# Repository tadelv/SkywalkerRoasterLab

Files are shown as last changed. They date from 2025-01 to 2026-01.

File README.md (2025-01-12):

# Skywalker Roaster

This is a guide to for connecting the Skywalker/ITOP MTCR(SkItop) Roaster connected to Artisan. In addition to the arduino sketches the data I've collected about the roaster is available here.

⚠️WARNING 👉 DO NOT LEAVE ROASTER UNATTENDED⚠️

The easiest way to get this working is to
1. Connect USB cable to [Arduino](#arduino-instructions) with correct jumpers
2. Load [Sketch](#arduino-instructions) onto arduino
3. Load [config[](#artisan-upload-config) into artisan-scope
4. Plug in arduino to computer through arduino USB cable(NOT the one we jumpered)
5. Plug in arduino to roaster where the controller was connected with the USB cable we jumpered
6. In artisan [config](#artisan-manually-setting-config) set the correct device
7. click/tap the on button in artisan-scope and temps should be available and roaster is controllable
   
## Arduino Sketches

### SkyCommand
This is full control of the skywalker roaster via Artisan. The sketch does the bare minimum to emulate TC4. Exercise caution, there are minimal safety features built in. As with every other coffee roaster..

⚠️WARNING 👉 DO NOT LEAVE ROASTER UNATTENDED⚠️

The sketch requires that it see a command from Artisan at least every 10 seconds or it will shut down. The READ commands from artisan will keep it going. I think it's ok to run, but what do I know? I'm just a nerd on the internet. Use this at your own risk.

#### Hardware
I use an arduino leonardo with a USB cable soldered to the Vin, GND, and Digital Pins 2 and 3. That's it.
PXL_20231206_190446798 MP

The black cable goes to the USB port on the back of the roaster (that's only USB in form.. it's not actually using USB communications), the white one to my computer running Artisan.

## Arduino Instructions

1. Install ArduinoIDE

2. Find any old USB cable. Cut it up in half, and prune a bit off the plastic sleeving. You should find four smaller wires. Connect these wires to your Arduino as such either through soldering or just inserting it into the slots:

      Green -> Digital 2  
      White -> Digital 3  
      Red -> VIN  
      Black -> GND

    Breadboard example:
   
    

    Soldering example (more secure):
   
    
    
    
3. Download repository and extract.


1. Connect your Arduino into your computer.

    

2. Go to your SkywalkerRoaster-main folder that you extracted. Click on the SkyCommand folder then double click on `SkyCommand.ino` (should open automatically in ArduinoIDE)

3. Click on the check mark to do a precompile, this lets you know if the code will work on your board.
4.  Click on your Arduino device and press Upload, the console on the bottomr should give you a success message. Some boards output debug, but if there is no error it probably succeeded.


## Hardware Pinout Examples
Arduino Micro
<!-- <img src="images/ardunio_micro_pinout.jpg" alt="micro pinout" width="400"/> -->


## Artisan Upload Config
We can upload a preset config in Artisan Scope
Help -> Load Settings...


This is a default file with the most basic settings.
[basic-skitop-artisan-settings.aset](ArtisanConfigs/basic-skitop-artisan-settings.aset)

look in [ArtisanConfigs](ArtisanConfigs/) for other configs users have created.

## Artisan Manually Setting Config
Here's how I have Artisan configured.
Config -> Device


After pressing OK, an additional dialogue box will appear, select your Arduino. If you're not sure which is your Arduino, disconnect and reconnect it and the dialogue box should change.
You can also navigate here by going to Config -> Port...
Comm Port will be different depending on OS you are running and which USB port you are plugged into.



Config -> Events -> Config

```
DRUM;100
```

Config -> Events -> Buttons

```
DRUM;100
```
```
DRUM;0
```
```
FILTER;1
```
etc..

Config -> Events -> Sliders

```
OT2;{}
```
```
OT1;{}
```
### Troubleshooting
- check all connections, unplug and re-plug in the USB cables, also check pins and solder points
- swap out USB cables, the arduino to computer cable is important also
- you will need to have drivers for your arduino unit on some machines so if you're running on a different machine where you set up the arduino, just install arduino IDE and install the drivers with the IDE to ensure you can connect
- make sure you are on the tested or later version of artisan

### Testing/Compatibility
#### Artisan Version
- 2.10.2
#### Working Hardware Combos
- Leonardo
  - Windows ?
- Micro
  - Windows 11
  - MacOS
- Nano ATMEGA
  - Linux Mint

- Uno Wifi R4
  - not yet

### SkywalkerSpy
This provides logging only for Artisan. It uses two pins to monitor the Tx lines from both the roaster and the controller. It alternates between reading the values as quickly as possible. When any input comes in on the serial line the sketch will respond with the status of the roaster in the format TEMP,HEAT DUTY,VENT DUTY

## Roaster Hardware
This has been super fun to study. Here's what I've learned so far.

The controller has a [js32t031f5s7 microcontoller](http://www.honor-ic.com/Product/ProScreenDetail?pid=118).

I am unsure what kind of microcontroller is inside the roaster. It is marked FMD N3hWIKH and I was unable to locate any datasheets for it.



The roaster uses a thermistor as a temperature probe which is connected to the microcontroller as shown here.



It appears to use a voltage divider with two taps, one passing through a 1k resistor and the other through a 2k resistor. I'm not the strongest hardware guy by any means, but I don't understand why. If this look familiar to you, please let me know what we're looking at here.

### Normal Operation
The Skywalker roaster is rather simple all logic lives in the controller. The roaster simply interprets the signals sent by the controller and sets things accordingly. The roaster appears to shut down if it does not receive a control message in 1 second. The controller reads the temperature values from the roaster and then sends instructions to the roaster. There does not appear to be any kind of communications protocol, each device appears to send messages to the other device roughly every 10 milliseconds. There are no requests, responses, acknowledgements, etc..  Simply data bit banged on a GPIO line.

## Messages
The messages sent by each device are rather simple in structure. I've determined what most everything does. To the logic analyzer, the messages appear as follows. This is an example of the message the roaster sends. The controller's messages look identical other than being 8 bits shorter.



Interpreting the messages can be done by simply measuring the logic LOW pulses. The beginning preamble is roughly 7.5ms, a binary 1 is represented by a ~1.5ms pulse, a binary 0 is ~600 microseconds, and the logic HIGH between bits is roughly 750 microseconds.



### Controller
The controller transmits a 6 byte message in LSB order. Both messages contain a checksum and will be ignored if the checksum is not correct.

| Position | Purpose | Value |
|---|---|---|
| 0 | Fan Duty Cycle | 0 to 100
| 1 | Filter | Appears to only be values 0,1,2,3,4 |
| 2 | Bean Cooling Fan | 0 or 100 |
| 3 | Drum | 0 or 100 |
| 4 | Heater Duty Cylce | 0 to 100 |
| 5 | Checksum | |

For the Fan and Heater, duty cycles increment by 5. Sending other values will be ignored.

### Roaster
The roaster transmits a 7 byte message in LSB Order.
|Position| Name| Value|
|---|-----|---|
|0,1| Value A | I'm not _really_ sure what this value is. I suspect it is perhaps a voltage as read by an ADC on the microcontroller|
|2,3|Value B|Again, not _really_ sure what the value really represents. I think it is another ADC value.|  
| 4 | Mystery byte | Always a 0.|
| 5 | Mystery byte | Pretty much always a 1. I've not seen much of a correlation to hardware that seems to indicate what this may represent.|
|6 | Checksum||

Value A and Value B are my biggest open question about this roaster. What is it doing?! There is a very strong linear correlation between the two values and the temperature displayed on the controller screen. However I could not determine what I would consider to be an "elegant" solution for converting these values to the temperature. Rather, I fit a 4th degree polynomial to the data (see `data/model3.py` but please keep in mind it's been a long minute since I've run a regression. ChatGPT wrote a lot of that with some guidance.)

To collect the data I attached a logic probe to the controller and captured a preheat cycle. I extracted all the messages from the capture, wrote an arduino sketch to replay the bytes in the messages back to the controller, and coded up a quick and dirty python script to push each message to the arduino and allow me to enter the value shown on the screen. The results of this process are in `Data/RealLabeledTemperatures.txt`

### Other Observations
- The roaster is looking for a USB ground, if nothing is there it will not run, if you unplug the controller or arduino during a roast, everything shuts down, this is actually kind of dangerous as the beans inside could ignite without movement or fan.
- Some testing unplugging the signal pins in the arduino yielded that the roaster will not run without constant signals from these pins either, but the user can plug back in and start controlling the roaster again. (granted you don't hit the 10sec limit from the sketch)

# Discord

There's a skywalker specific discord (not mine) that seems to have a small but growing and enthusiastic group. I'm on there. Come share your experiences with this roaster. [Skywalker Roaster Community](https://discord.gg/m4TtNRb4uc)

# Bug Fixes and Improvements

I'll spend some more time on things when I can, but pull requests are always welcome and appreciated.

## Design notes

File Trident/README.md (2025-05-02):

# Trident for Skywalker

Combines BLE, USB and WiFi access to the Skywalker roaster in one controller.

# Supported boards:

[ESP32-S3 devkitc 1 (dual usb-c)](https://a.aliexpress.com/_EH8OGvc)

# BLE setup
Use HiBean to connect to Trident. Search for "Skywalker-Trident" when adding the roaster in HiBean app.

# USB setup
Use the left usb-c port (when the board is facing you, usb ports facing down), to connect it to your computer. Use one
of the provided `.aset` Artisan settings in the "Artisan Config" folder, to connect to the roaster. Remember to select the correct port in Artisan!

# Wifi setup
At first start, Trident creates an access point with the SSID "Trident". Once you connect to it, you can use the
provided artisan config (in this folder) and it should connect automatically.

If you wish to setup Trident to connect to your home Wifi, you can set it up using a simple curl command or by visiting
the address in the browser:
```
curl http://trident.local/api/wifi?ssid=<your-wifi>&pass=<your-pass>
```

This will save the wifi ssid and credentials to Trident persistent storage. Now you can reboot/reset Trident and it will
connect to your Wifi automatically. 
If Trident can't find the specified Wifi or the password is incorrect, it will create the previously mentioned access
point, so that you can change the wifi data again.

# Simultaneous operation
While not entirely sensible, simultaneous operation is theoretically possible with Trident. You could for example
observe and control the roast, both from HiBean and Artisan at the same time.

# TODO list:

- PID control
- LED status signalling
- code cleanup and potential improvements

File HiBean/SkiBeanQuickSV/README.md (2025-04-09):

# PID Commands - HiBean ESP32 BLE Roaster Control

This document lists the available commands for controlling the roaster using PID_v1 in the HiBean ESP32 BLE Roaster Control firmware.

## **PID Commands & Behavior**
The **PID_v1** library is used to regulate heating power based on the measured temperature. It operates in **two modes**:
- **Automatic (PID ON):** Uses PID logic to adjust the heater output.
- **Manual (PID OFF):** Allows manual control of heater power.

## **Available Commands (case-INsensitive)**
| **Command** | **Description** |
|---|---|
| `PID;ON` | Enables PID control (automatic mode). |
| `PID;OFF` | Disables PID control (switches to manual mode). |
| `PID;SV;XXX` | Sets the PID **setpoint temperature** (XXX is in °C, e.g., `PID;SV;250` sets the target to 250°C). |
| `PID;T;PP.P;II.I;DD.D` |  Apply provided tunings to the PID control (not persisted). |
| `PID;CT;XXX` | Temporarily sets PID cycle (sample) time to XXXms (not persisted). |
| `PID;PM;E` | Temporarily change pMode: E = P_ON_E to M = P_ON_M(default), or reverse (not persisted). |
| `OT1;XX` | Manually sets heater power to **XX%** (only works in MANUAL mode). |
| `READ` | Retrieves current temperature, set temperature, heater, and vent power. |

## **Other Control Commands**
| **Command** | **Description** |
|---|---|
| `OT2;XX` | Sets the vent power to **XX%**. |
| `OFF` | Shuts down the system. |
| `ESTOP` | Emergency stop: Sets heater to 0% and vent to 100%. |
| `DRUM;XX` | Starts/stops the drum motor (1 = ON, 0 = OFF). |
| `FILTER;XX` | Controls filter fan power (1 fastest - 4 slowest; 0 off). |
| `COOL;XX` | Activates cooling function (0-100%). |
| `CHAN` | Sends active channel configuration. |
| `UNITS;C/F` | Sets temperature units to **Celsius (C)** or **Fahrenheit (F)**. |

## **Usage Example**
- Enable PID control:
  ```
  PID;ON
  ```
- Set target temperature to 250°C:
  ```
  PID;SV;250
  ```
- Manually set heater to 70% power:
  ```
  OT1;70
  ```
- Read current system status:
  ```
  READ
  ```

This document serves as a quick reference for controlling the roaster over BLE using the HiBean ESP32 BLE Roaster Control firmware.

TODO
- ~~BLE on Core1~~
- PID storage via Preference
- sTune Autotune Function
- RTD Max31865 Implementation
- TC Max31855 Implementation
- AutoDrop Servo

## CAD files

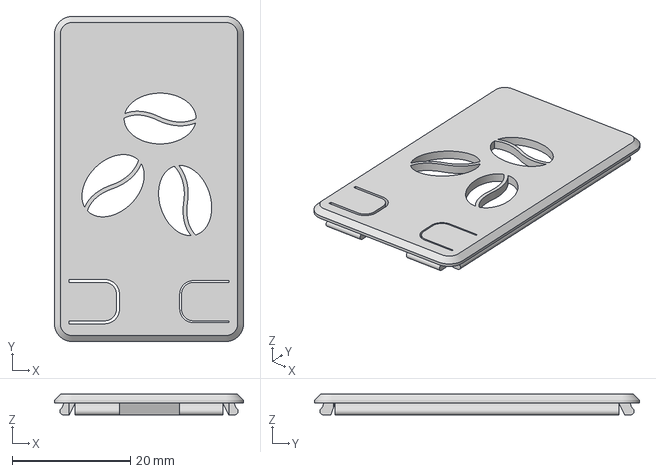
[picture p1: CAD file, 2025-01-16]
HiBean/3DP Case/SkiBeanMiniLid.3mf
32.0 x 55.0 x 3.50 mm

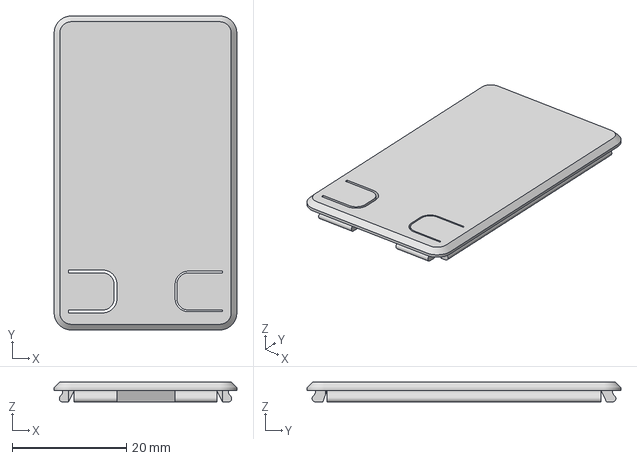
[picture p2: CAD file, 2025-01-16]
HiBean/3DP Case/SkiBeanMiniLid_nobnz.3mf
32.0 x 55.0 x 3.50 mm

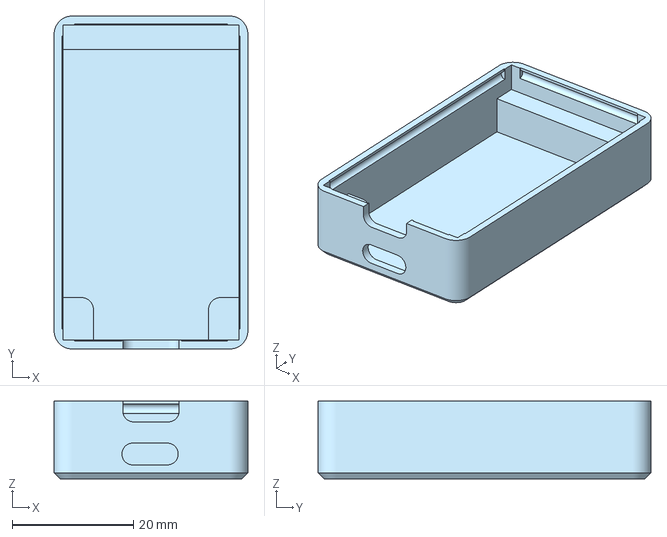
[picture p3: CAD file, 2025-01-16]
HiBean/3DP Case/SkiBeanMiniCase.3mf
32.0 x 55.0 x 12.8 mm

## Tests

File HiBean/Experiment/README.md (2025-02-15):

# QuickPID Commands - HiBean ESP32 BLE Roaster Control

This document lists the available commands for controlling the roaster using QuickPID in the HiBean ESP32 BLE Roaster Control firmware.

## **PID Commands & Behavior**
The **QuickPID** library is used to regulate heating power based on the measured temperature. It operates in **two modes**:
- **Automatic (PID ON):** Uses PID logic to adjust the heater output.
- **Manual (PID OFF):** Allows manual control of heater power.

## **Available Commands**
| **Command** | **Description** |
|---|---|
| `PID;ON` | Enables PID control (automatic mode). |
| `PID;OFF` | Disables PID control (switches to manual mode). |
| `PID;SV;XXX` | Sets the PID **setpoint temperature** (XXX is in °C, e.g., `PID;SV;250` sets the target to 250°C). |
| `OT1;XX` | Manually sets heater power to **XX%** (only works in MANUAL mode). |
| `READ` | Retrieves current temperature, set temperature, heater, and vent power. |

## **Other Control Commands**
| **Command** | **Description** |
|---|---|
| `OT2;XX` | Sets the vent power to **XX%**. |
| `OFF` | Shuts down the system. |
| `ESTOP` | Emergency stop: Sets heater to 0% and vent to 100%. |
| `DRUM;XX` | Starts/stops the drum motor (1 = ON, 0 = OFF). |
| `FILTER;XX` | Controls filter fan power (0-100%). |
| `COOL;XX` | Activates cooling function (0-100%). |
| `CHAN` | Sends active channel configuration. |
| `UNITS;C/F` | Sets temperature units to **Celsius (C)** or **Fahrenheit (F)**. |

## **Usage Example**
- Enable PID control:
  ```
  PID;ON
  ```
- Set target temperature to 250°C:
  ```
  PID;SV;250
  ```
- Manually set heater to 70% power:
  ```
  OT1;70
  ```
- Read current system status:
  ```
  READ
  ```

This document serves as a quick reference for controlling the roaster over BLE using the HiBean ESP32 BLE Roaster Control firmware.

TODO
- BLE on Core1
- PID storage via Preference
- sTune Autotune Function
- RTD Max31865 Implementation
- TC Max31855 Implementation
- AutoDrop Servo

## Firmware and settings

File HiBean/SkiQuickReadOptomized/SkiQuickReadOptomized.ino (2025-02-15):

/***************************************************

HiBean ESP32 BLE Roaster Control

Replaces Classic Bluetooth with BLE (NUS).

Service UUID:

6e400001-b5a3-f393-e0a9-e50e24dcca9e

Characteristics UUIDs:

Write Characteristic (RX):


6e400002-b5a3-f393-e0a9-e50e24dcca9e

Notify Characteristic (TX):


6e400003-b5a3-f393-e0a9-e50e24dcca9e

Sends notifications for temperature/status data.

Expects commands via the write characteristic.


***************************************************/

#include <Arduino.h>

#include <BLEDevice.h>

#include <BLEUtils.h>

#include <BLEServer.h>

#include <BLE2902.h>

#include <QuickPID.h>

#include <sTune.h>
#include <Preferences.h>  // For saving PID settings



// -----------------------------------------------------------------------------

// BLE UUIDs for Nordic UART Service

// -----------------------------------------------------------------------------

#define SERVICE_UUID           "6e400001-b5a3-f393-e0a9-e50e24dcca9e" // NUS service

#define CHARACTERISTIC_UUID_RX "6e400002-b5a3-f393-e0a9-e50e24dcca9e" // Write

#define CHARACTERISTIC_UUID_TX "6e400003-b5a3-f393-e0a9-e50e24dcca9e" // Notify

// -----------------------------------------------------------------------------

// BLE Globals

// -----------------------------------------------------------------------------

BLEServer* pServer = nullptr;

BLECharacteristic* pTxCharacteristic = nullptr;

bool deviceConnected = false;

TaskHandle_t bleTaskHandle;

bool tuningActive = false;

sTune* tuner; 

Preferences preferences;

// -----------------------------------------------------------------------------

// Pin Definitions

// -----------------------------------------------------------------------------

const int TX_PIN = 19;  // Output pin to roaster

const int RX_PIN = 20;  // Input pin from roaster

// -----------------------------------------------------------------------------

// Timing Constants

// -----------------------------------------------------------------------------

const int PREAMBLE        = 7000;

const int PULSE_ONE       = 1200;

const int PULSE_ZERO      = 650;

const int POST_PULSE_DELAY= 750;

const int START_PULSE     = 7500;

const int START_DELAY     = 3800;

// -----------------------------------------------------------------------------

// Buffer Sizes

// -----------------------------------------------------------------------------

const int ROASTER_LENGTH    = 7;   // 7 bytes received from roaster

const int CONTROLLER_LENGTH = 6;   // 6 bytes sent to roaster

// -----------------------------------------------------------------------------

// Control Byte Indices

// -----------------------------------------------------------------------------

enum ControlBytes {

VENT_BYTE = 0,

DRUM_BYTE = 3,

COOL_BYTE = 2,

FILTER_BYTE = 1,

HEAT_BYTE = 4,

CHECK_BYTE = 5

};

uint8_t receiveBuffer[ROASTER_LENGTH];

uint8_t sendBuffer[CONTROLLER_LENGTH];

// Raw temperature values

uint16_t rawTempX, rawTempY;

// Control Bytes & Checksum

void setControlChecksum() {

uint8_t sum = 0;

for (int i = 0; i < (CONTROLLER_LENGTH - 1); i++) {

    sum += sendBuffer[i];

}

sendBuffer[CHECK_BYTE] = sum;  // Correct use of CHECK_BYTE

}

void setValue(uint8_t* bytePtr, uint8_t value) {

*bytePtr = value;

setControlChecksum();

}

// -----------------------------------------------------------------------------

// Temperature Variables & Filter

// -----------------------------------------------------------------------------

double temp          = 0.0;           // Filtered temperature

unsigned long lastEventTime = 0;

const unsigned long LAST_EVENT_TIMEOUT = 10UL * 1000000UL; // 10 seconds (micros)

char CorF            = 'C';           // 'C' or 'F'

int filtWeight       = 80;            // Filter weight (Artisan default)

// Define PID variables

float setpoint = 250.0; // Desired temperature (adjustable)

float input, output;

double Kp = 15, Ki = 0.070, Kd = .060;

QuickPID myPID(&input, &output, &setpoint, Kp, Ki, Kd, QuickPID::pMode::pOnError, QuickPID::dMode::dOnMeas, QuickPID::iAwMode::iAwCondition, QuickPID::Action::direct);

int manualHeatLevel = 50;

// -----------------------------------------------------------------------------

// Command Strings

// -----------------------------------------------------------------------------

const String CMD_READ         = "READ";

const String CMD_HEAT         = "OT1";

const String CMD_VENT         = "OT2";

const String CMD_OFF          = "OFF";

const String CMD_DRUM         = "DRUM";

const String CMD_FILTER       = "FILTER";

const String CMD_COOL         = "COOL";

const String CMD_CHAN         = "CHAN";

const String CMD_UNITS        = "UNITS";

const String CMD_FILTER_WEIGHT= "FILT";

// -----------------------------------------------------------------------------

// Forward Declarations

// -----------------------------------------------------------------------------

void parseAndExecuteCommands(String input);

void executeCommand(String command, uint8_t value);

void shutdown();

void sendMessage();

void getRoasterMessage();

// -----------------------------------------------------------------------------

// BLE Server Callbacks

// -----------------------------------------------------------------------------

class MyServerCallbacks : public BLEServerCallbacks {

void onConnect(BLEServer* pServer) override {

deviceConnected = true;

Serial.println("BLE: Client connected.");

}

void onDisconnect(BLEServer* pServer) override {

deviceConnected = false;

Serial.println("BLE: Client disconnected. Restarting advertising...");

pServer->getAdvertising()->start();

}

};

// -----------------------------------------------------------------------------

// BLE Characteristic Callbacks

// -----------------------------------------------------------------------------

class MyCallbacks : public BLECharacteristicCallbacks {

void onWrite(BLECharacteristic* pCharacteristic) override {

String rxValue = String(pCharacteristic->getValue().c_str());



if (rxValue.length() > 0) {

  String input = String(rxValue.c_str());

  Serial.print("BLE Write Received: ");

  Serial.println(input);

  parseAndExecuteCommands(input);

}

}

};

// -----------------------------------------------------------------------------

// Utility Functions

// -----------------------------------------------------------------------------

bool itsbeentoolong() {

unsigned long now = micros();

unsigned long duration = now - lastEventTime;

return (duration > LAST_EVENT_TIMEOUT);

}

void notifyClient(const String& message) {
    static unsigned long lastNotify = 0;
    const unsigned long notifyInterval = 250; // 500ms delay

    if (millis() - lastNotify >= notifyInterval) {
        lastNotify = millis();
        
        Serial.println("Attempting to notify BLE client with: " + message);
        if (deviceConnected && pTxCharacteristic) {
            pTxCharacteristic->setValue(message.c_str());
            pTxCharacteristic->notify();
            Serial.println("Notification sent successfully.");
        } else {
            Serial.println("Notification failed. Device not connected or TX characteristic unavailable.");
        }
    }
}


void shutdown() {

Serial.println("Shutting down...");

for (int i = 0; i < CONTROLLER_LENGTH; i++) {

    sendBuffer[i] = 0;

}

sendBuffer[CHECK_BYTE] = 0; // Reset checksum

}

void sendMessage() {

// Start pulse

pulsePin(TX_PIN, START_PULSE);

delayMicroseconds(START_DELAY);



// Send each byte, bit by bit

for (int i = 0; i < CONTROLLER_LENGTH; i++) {

    for (int j = 0; j < 8; j++) {

        if (bitRead(sendBuffer[i], j) == 1) {

            // '1' bit

            pulsePin(TX_PIN, 1500);

        } else {

            // '0' bit

            pulsePin(TX_PIN, PULSE_ZERO);

        }

        delayMicroseconds(POST_PULSE_DELAY);

    }

}

}

void bleTask(void* parameter) {

Serial.println("Starting BLE task on Core 0...");



BLEDevice::init("ESP32_Skycommand_BLE");

BLEDevice::setMTU(250);



pServer = BLEDevice::createServer();

pServer->setCallbacks(new MyServerCallbacks());



BLEService* pService = pServer->createService(SERVICE_UUID);



pTxCharacteristic = pService->createCharacteristic(

    CHARACTERISTIC_UUID_TX,

    BLECharacteristic::PROPERTY_NOTIFY | BLECharacteristic::PROPERTY_READ

);

pTxCharacteristic->addDescriptor(new BLE2902());



BLECharacteristic* pRxCharacteristic = pService->createCharacteristic(

    CHARACTERISTIC_UUID_RX,

    BLECharacteristic::PROPERTY_WRITE | BLECharacteristic::PROPERTY_WRITE_NR

);

pRxCharacteristic->setCallbacks(new MyCallbacks());

pRxCharacteristic->addDescriptor(new BLE2902());



pService->start();

pServer->getAdvertising()->start();

Serial.println("BLE Advertising started...");



for (;;) { 


    vTaskDelay(1000 / portTICK_PERIOD_MS); // Run every 1s

}

}

void pulsePin(int pin, int duration) {

digitalWrite(pin, LOW);

delayMicroseconds(duration);

digitalWrite(pin, HIGH);

}

void getRoasterMessage() {

bool passedChecksum = false;

// Keep trying until a valid checksum is found

while (!passedChecksum) {

    getMessage(ROASTER_LENGTH, RX_PIN);

    passedChecksum = calculateRoasterChecksum();

}

// Once valid, compute temperature with filtering

filtTemp(calculateTemp());

}

void getMessage(int bytes, int pin) {

unsigned long timeIntervals[ROASTER_LENGTH * 8];

unsigned long pulseDuration = 0;

int bits = bytes * 8;



// Wait for a pulse >= PREAMBLE

while (pulseDuration < PREAMBLE) {

    pulseDuration = pulseIn(pin, LOW);

}



for (int i = 0; i < bits; i++) {

    timeIntervals[i] = pulseIn(pin, LOW);

}



for (int i = 0; i < bytes; i++) {

    receiveBuffer[i] = 0;

}



for (int i = 0; i < bits; i++) {

    if (timeIntervals[i] > PULSE_ONE) {

        receiveBuffer[i / 8] |= (1 << (i % 8));

    }

}

}

bool calculateRoasterChecksum() {

uint8_t sum = 0;

for (int i = 0; i < (ROASTER_LENGTH - 1); i++) {

    sum += receiveBuffer[i];

}

return (sum == receiveBuffer[ROASTER_LENGTH - 1]);

}

double calculateTemp() {

rawTempX = ((receiveBuffer[0] << 8) + receiveBuffer[1]);

rawTempY = ((receiveBuffer[2] << 8) + receiveBuffer[3]);



double x = 0.001 * rawTempX;

double y = 0.001 * rawTempY;

double v;  // Declare v here



if (rawTempX > 836 || rawTempY > 221) {

    v = -224.2 * y * y * y + 385.9 * y * y - 327.1 * y + 171;

} else {

    v = -278.33 * x * x * x + 491.944 * x * x - 451.444 * x + 310.668;

}



if (CorF == 'F') {

    v = 1.8 * v + 32.0;

}

return v;

}

void filtTemp(double v) {

if (fabs(temp - v) > 10.0) {

    temp = v;

} else {

    temp = (v * (100.0 - filtWeight) + temp * filtWeight) / 100.0;

}

}

void handleCHAN() {
  String message = "# Active channels set to 2100\r\n";
Serial.println(message);

notifyClient(message);

}

//Quickpid hControls///

//adjusting the heating power based on PID temperature control

void handlePIDControl() {
    static unsigned long lastPIDUpdate = 0;
    const unsigned long pidInterval = 250; // 250ms update rate

    if (millis() - lastPIDUpdate >= pidInterval) {
        lastPIDUpdate = millis();
        
        if (myPID.GetMode() == static_cast<uint8_t>(QuickPID::Control::automatic)) {
            input = temp;  // Update PID input
            myPID.Compute();
            int heatValue = constrain(output, 0, 100);
            handleHEAT(heatValue);
        } else {
            handleHEAT(manualHeatLevel);
        }
    }
}


void setPIDMode(bool usePID) {

if (usePID) {

    myPID.SetMode(QuickPID::Control::automatic); // Enable PID

    Serial.println("PID mode set to AUTOMATIC");

} else {

    myPID.SetMode(QuickPID::Control::manual); // Disable PID

    manualHeatLevel = 0;  // Set heat to 0% for safety

    handleHEAT(manualHeatLevel); // Apply the change immediately

    Serial.println("PID mode set to MANUAL");

}

}

void handleOT1(uint8_t value) {

if (myPID.GetMode() == static_cast<uint8_t>(QuickPID::Control::manual)) {

    manualHeatLevel = constrain(value, 0, 100); // Set manual heat level

    handleHEAT(manualHeatLevel); // Apply the new setting

}

}

void handleREAD() {
    if (!deviceConnected) {
        Serial.println("⚠️ READ failed: No BLE connection.");
        return;
    }

    String output = "0," + String(temp, 1) + "," + String(temp, 1) + "," +
                    String(sendBuffer[HEAT_BYTE]) + "," +
                    String(sendBuffer[VENT_BYTE]) + "\r\n";

    Serial.println("📡 Sending READ Output: " + output);

    // ✅ IMMEDIATELY send BLE notification
    pTxCharacteristic->setValue(output.c_str());
    pTxCharacteristic->notify();
    
    Serial.println("✅ READ notification sent!");

    lastEventTime = micros();
}

void handleHEAT(uint8_t value) {

if (value <= 100) {

    setValue(&sendBuffer[HEAT_BYTE], value);

}

lastEventTime = micros();

}

void handleVENT(uint8_t value) {

if (value <= 100) {

    setValue(&sendBuffer[VENT_BYTE], value);

}

lastEventTime = micros();

}

void handleDRUM(uint8_t value) {

if (value != 0) {

    setValue(&sendBuffer[DRUM_BYTE], 100);

} else {

    setValue(&sendBuffer[DRUM_BYTE], 0);

}

lastEventTime = micros();

}

void handleFILTER(uint8_t value) {

if (value <= 100) {

    setValue(&sendBuffer[FILTER_BYTE], value);

}

lastEventTime = micros();

}

void handleCOOL(uint8_t value) {

if (value <= 100) {

    setValue(&sendBuffer[COOL_BYTE], value);

}

lastEventTime = micros();

}

void eStop() {

Serial.println("Emergency Stop Activated! Heater OFF, Vent 100%");

handleHEAT(0);   // Turn off heater

handleVENT(100); // Set vent to 100%

}

void parseAndExecuteCommands(String input) {
    input.trim();
    Serial.println("Parsing command: " + input);

    int split1 = input.indexOf(';');
    String command = "";
    String param = "";
    String subcommand = "";

    if (split1 >= 0) {
        command = input.substring(0, split1);
        String remainder = input.substring(split1 + 1);
        int split2 = remainder.indexOf(';');

        if (split2 >= 0) {
            subcommand = remainder.substring(0, split2);
            param = remainder.substring(split2 + 1);
        } else {
            param = remainder;
        }
    } else {
        command = input;
    }

    if (command == "PID") {
        if (param == "ON") {
            setPIDMode(true);  // ✅ Enable PID control
        } else if (param == "OFF") {
            setPIDMode(false); // ✅ Disable PID control
        } else if (subcommand == "SV") {
            double newSetpoint = param.toDouble();
            if (newSetpoint > 0 && newSetpoint <= 300) {  // Example range check
                setpoint = newSetpoint;
                Serial.print("✅ New Setpoint: ");
                Serial.println(setpoint);
            }
        }
    } else if (command == "OT1") {  
        uint8_t value = param.toInt();
        handleOT1(value);  // ✅ Manual heater control (only in MANUAL mode)
    } else if (command == "READ") {
        handleREAD();
    } else if (command == "OT2") {  
        handleVENT(param.toInt());  // ✅ Set fan duty
    } else if (command == "OFF") {  
        shutdown();  // ✅ Shut down system
    } else if (command == "ESTOP") {  
        eStop();  // ✅ Emergency stop (heater = 0, vent = 100)
    } else if (command == "DRUM") {  
        handleDRUM(param.toInt());  // ✅ Start/stop the drum
    } else if (command == "FILTER") {  
        handleFILTER(param.toInt());  // ✅ Turn on/off filter fan
    } else if (command == "COOL") {  
        handleCOOL(param.toInt());  // ✅ Cool the beans
    } else if (command == "CHAN") {  
        handleCHAN();  // ✅ Handle TC4 init message
    } else if (command == "UNITS") {  
        if (split1 >= 0) CorF = input.charAt(split1 + 1);  // ✅ Set temperature units
    } else if (command == "AUTOTUNE") {  
        startAutoTune();  // ✅ Start PID AutoTune
    }
}


void loadPIDPreferences() {
    preferences.begin("PID", false);  // Open namespace "PID"
    Kp = preferences.getFloat("Kp", 15.0);  // Default value if not set
    Ki = preferences.getFloat("Ki", 0.070);
    Kd = preferences.getFloat("Kd", 0.060);
    preferences.end();

    Serial.printf("✅ Loaded PID Values: Kp=%.3f, Ki=%.3f, Kd=%.3f\n", Kp, Ki, Kd);
}

void savePIDPreferences(float newKp, float newKi, float newKd) {
    preferences.begin("PID", false);
    preferences.putFloat("Kp", newKp);
    preferences.putFloat("Ki", newKi);
    preferences.putFloat("Kd", newKd);
    preferences.end();
    
    Serial.printf("✅ New PID Values Saved: Kp=%.3f, Ki=%.3f, Kd=%.3f\n", newKp, newKi, newKd);
}

void startAutoTune() {
    Serial.println("AUTOTUNE command received, but tuning is disabled for debugging.");
}


void handleAutoTune() {
    if (!tuningActive) return;

    switch (tuner->Run()) {
        case sTune::sample:
            Serial.println("AutoTune Sampling...");
            break;

        case sTune::tunings:
            float newKp, newKi, newKd;
            tuner->GetAutoTunings(&newKp, &newKi, &newKd);
            Serial.printf("AutoTune Complete: Kp=%.3f, Ki=%.3f, Kd=%.3f\n", newKp, newKi, newKd);

            savePIDPreferences(newKp, newKi, newKd);
            myPID.SetTunings(newKp, newKi, newKd);

            tuningActive = false;
            break;
    }
}





void setup() {
    Serial.begin(115200);
    Serial.println("🚀 Starting HiBean ESP32 BLE Roaster Control...");

    pinMode(TX_PIN, OUTPUT);
    digitalWrite(TX_PIN, HIGH);
    pinMode(RX_PIN, INPUT);

    //  Start BLE
    BLEDevice::init("ESP32_Skycommand_BLE");
    BLEDevice::setMTU(250);

    //  Start BLE task on Core 0
    xTaskCreatePinnedToCore(
        bleTask,       
        "BLE Task",    
        10000,         
        NULL,          
        configMAX_PRIORITIES - 1,  
        NULL,          
        0              
    );

    delay(1000);  //  Allow BLE to stabilize

    //  Load previously saved PID values
    loadPIDPreferences();

    //  Set PID with loaded values
    myPID.SetTunings(Kp, Ki, Kd);

    myPID.SetMode(QuickPID::Control::manual);
    
    manualHeatLevel = 0;
    handleHEAT(manualHeatLevel);
    
    shutdown();
}



//void loop() {

//if (itsbeentoolong()) {

//     shutdown();

//  }

// sendMessage();

//    getRoasterMessage();

// Ensure PID or manual heat control is handled

  // handlePIDControl();

//}

unsigned long lastWriteTime = 0;
const unsigned long writeInterval = 100;  // 100ms between writes

const unsigned long readInterval = 1000; // Read every 1 second
unsigned long lastReadTime = 0;

void loop() {
    if (itsbeentoolong()) {
        shutdown();
    }

    if (!deviceConnected) {  
        Serial.println("⚠️ BLE Disconnected: Restarting Advertising...");
        pServer->startAdvertising();
    }

    if (tuningActive) {
        handleAutoTune();
    } else {
        // ✅ PRIORITIZE `READ` FIRST (Runs every 500ms instead of 1s)
        if (millis() - lastReadTime >= 250) {  
            handleREAD();
            lastReadTime = millis();
        }

        // ✅ Prevent `getRoasterMessage()` from blocking BLE
        unsigned long startTime = millis();
        getRoasterMessage();
        if (millis() - startTime > 150) {  // If it takes too long, print warning
            Serial.println("⚠️ getRoasterMessage() took too long!");
        }

        // ✅ Make sure PID control doesn't slow down BLE
        handlePIDControl();

        // ✅ Ensure `sendMessage()` runs efficiently
        if (millis() - lastWriteTime >= 100) { // Runs every 100ms
            sendMessage();
            lastWriteTime = millis();
        }
    }
}

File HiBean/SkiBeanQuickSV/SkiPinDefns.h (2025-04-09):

// -----------------------------------------------------------------------------
// Pin Definitions
// -----------------------------------------------------------------------------
#if SERIAL_DEBUG == 1
  const int TX_PIN = NULL;  // bogus pin
  const int RX_PIN = NULL;  // bogus pin
  const int LED_PIN = NULL; // bogus pin
  const String boardID_BLE = String("DEBUG");
#elif defined(ARDUINO_WAVESHARE_ESP32_S3_ZERO)
  const int TX_PIN = 19;  // Output pin to roaster
  const int RX_PIN = 20;  // Input pin from roaster
  const int LED_PIN = WS_RGB; // WaveShare S3 on-board LED
  const String boardID_BLE = String("ARDUINO_WAVESHARE_ESP32_S3_ZERO");
#elif defined(ARDUINO_ESP32C6_DEV)
  const int TX_PIN = 11;  // Output pin to roaster - use any free GPIO
  const int RX_PIN = 10;  // Input pin from roaster - use any free GPIO
  const int LED_PIN = PIN_RGB_LED; // rgb values in a different order for this board - not fixed
  const String boardID_BLE = String("ARDUINO_ESP32C6_DEV");
#else
  const int TX_PIN = 1;  // bogus pin
  const int RX_PIN = 2;  // bogus pin
  const int LED_PIN = 0; // bogus pin
  const String boardID_BLE = String("UNKNOWN");
#endif

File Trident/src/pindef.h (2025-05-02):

#ifndef PINDEF
#define PINDEF
#if defined(S3MINI) || defined(S3)
const int RX_PIN = 20;
const int TX_PIN = 19;
const int RGB_PIN = 48;
#else
const int RX_PIN = 13;
const int TX_PIN = 12;
const int RGB_PIN = 8;
#endif
#endif

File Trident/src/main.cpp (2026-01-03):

#include <Arduino.h>
#include <AsyncTCP.h>
#include <ESPAsyncWebServer.h>
#include <ESPmDNS.h>
#include <PID_v1.h>
#include <WiFi.h>

#include "CommandLoop.h"
#include "SkiComms.h"
#include "SkiCMD.h"
#include "api.h"
#include "ble.h"
#include "display.h"
#include "freertos/idf_additions.h"
#include "model.h"
#include "pindef.h"
#include "state_request_queue.h"
#include "wifi_setup.h"
#include "wifi_manager.h"
#include <esp_wifi.h>

// -----------------------------------------------------------------------------
// Global Bean Temperature Variable
// -----------------------------------------------------------------------------
double temp = 0.0; // Filtered temperature

// -----------------------------------------------------------------------------
// Define PID variables
// -----------------------------------------------------------------------------
double pInput, pOutput;
double pSetpoint = 0.0; // Desired temperature (adjustable on the fly)
int pMode = P_ON_M;
// was 20,1,3 at 1sec
// pid calibrations (adjustable on the fly)
double Kp = 20.0, Ki = 0.5, Kd = 4.0;
int pSampleTime = 1000; // ms (adjustable on the fly)
int manualHeatLevel = 0;
// pid instance with our default values
PID myPID(&pInput, &pOutput, &pSetpoint, Kp, Ki, Kd, pMode, DIRECT);

const unsigned int LED_BLUE[3] = {0, 0, 32};
const unsigned int LED_GREEN[3] = {0, 128, 0};
const unsigned int LED_RED[3] = {128, 0, 0};
const unsigned int LED_BLACK[3] = {0, 0, 0};
const unsigned int LED_YELLOW[3] = {0, 128, 128};

typedef enum { booting = 0, connected, disconnected } BloodhoundStateT;

AsyncWebServer server(80);
AsyncWebSocket
    wsConsole("/console"); // WebSocket for console (replaces WebSerial)
const char rgbLedPin = RGB_PIN;
// const char ledPin = 15;
bool isOn = false;
BloodhoundStateT m_state = booting;
void webSerialLoop(void *params);
void ledControl();

// Function to handle incoming console WebSocket messages
void handleConsoleMessage(AsyncWebSocketClient *client, uint8_t *data,
                          size_t len) {
  String input = String((char *)data, len);
  input.trim();

  // Echo the command back to the sender
  client->text("> " + input);

  // Parse and execute the command
  parseAndExecuteCommands(input);
}

void setup() {
  Serial.begin(115200);
  delay(100);
  pinMode(rgbLedPin, OUTPUT);

  rgbLedWrite(rgbLedPin, LED_RED[0], LED_RED[1], LED_RED[2]);

  initStateQueue();
  setupWifi();

  // Start WiFi monitoring for automatic reconnection
  startWiFiMonitor();

  // Setup console WebSocket (replaces WebSerial)
  wsConsole.onEvent([](AsyncWebSocket *server, AsyncWebSocketClient *client,
                       AwsEventType type, void *arg, uint8_t *data,
                       size_t len) {
    if (type == WS_EVT_CONNECT) {
      String welcome = "Console WebSocket Connected\n";
      welcome += "Type commands to control the system\n";
      welcome += "Use 'help' for available commands\n";
      welcome += "IP: " + WiFi.localIP().toString();
      client->text(welcome);
    } else if (type == WS_EVT_DATA) {
      AwsFrameInfo *info = (AwsFrameInfo *)arg;
      if (info->final && info->opcode == WS_TEXT) {
        handleConsoleMessage(client, data, len);
      }
    } else if (type == WS_EVT_DISCONNECT) {
      // Client disconnected
    }
  });
  server.addHandler(&wsConsole);

  setupMainLoop(&server);
  setupApi(&server);
  server.begin();
  // Increase stack size from 8192 to 12288 and priority from 1 to 2
  xTaskCreate(webSerialLoop, "WebSerialTask", 12288,
              NULL, 2, NULL);
  displayInit();
  myPID.SetOutputLimits(0, 95);

  // Configure WiFi/BLE coexistence for better stability
  esp_wifi_set_ps(WIFI_PS_MIN_MODEM);  // Minimum power save for better coexistence
  // Note: esp_coex_set_preference may not be available in all ESP32 framework versions
  // The WiFi power save setting above provides basic coexistence support

  // Let WiFi stabilize before starting BLE
  delay(2000);
  initBLE("Trident", "1.0.3", "Skywalker-Trident");

  pinMode(TX_PIN, OUTPUT);
  digitalWrite(TX_PIN, HIGH);
  pinMode(RX_PIN, INPUT);

  attachInterrupt(RX_PIN, watchRoasterStart, FALLING);

  shutdown();
}

StateRequestT _currentState = {0};
void webSocketLoop() {
  handleREAD();
  StateDataT data = {temp, _currentState};
  StateRequestT req = socketTick(data);
}

void bleLoop() {

  StateDataT data = {temp, _currentState};
  StateRequestT req = bleTick(data);
}

void serialLoop() {
  if (Serial.available() <= 0) {
    return;
  }
  String command = Serial.readStringUntil('\n');
  command.trim();
  CommandTypeT type = classifyCommandType(command);
  if (type == CMDType_READ) {
    // Use snprintf instead of String concatenation to prevent heap fragmentation
    char readMsg[64];
    snprintf(readMsg, sizeof(readMsg), "0,%.1f,%.1f,%d,%d\r\n",
             temp, temp, _currentState.heater, _currentState.fan);
    Serial.println(readMsg);
  } else if (type == CMDType_STATE_REQUEST) {
    StateRequestT req = parseCommandToStateRequest(command);
    enqueueStateRequest(req, SOURCE_USB);
  } else {
    parseAndExecuteCommands(command);
  }
}

void webSerialLoop(void *params) {
  static unsigned long lastStatusTime = 0;
  static unsigned long lastCleanupTime = 0;
  static unsigned long lastStackCheck = 0;
  static unsigned long lastHeapCheck = 0;
  const unsigned long STATUS_INTERVAL = 1000;  // Send status every 1 second
  const unsigned long CLEANUP_INTERVAL = 5000; // Cleanup every 5 seconds
  const unsigned long STACK_CHECK_INTERVAL = 60000; // Check stack every minute
  const unsigned long HEAP_CHECK_INTERVAL = 5000; // Check heap every 5 seconds

  while (1) {
    unsigned long now = millis();

#ifdef DEBUG
    // Monitor stack usage
    if (now - lastStackCheck > STACK_CHECK_INTERVAL) {
      UBaseType_t stackHighWater = uxTaskGetStackHighWaterMark(NULL);
      if (stackHighWater < 1024) {
        D_printf("WARNING: WebSerialTask low stack: %d bytes free\n", stackHighWater);
      }
      lastStackCheck = now;
    }
#endif

    // Monitor heap health
    if (now - lastHeapCheck > HEAP_CHECK_INTERVAL) {
      uint32_t freeHeap = ESP.getFreeHeap();
      uint32_t minFreeHeap = ESP.getMinFreeHeap();

      if (freeHeap < 80000) {  // Less than 80KB free
        D_printf("WARNING: Heap low - Free: %d, Min: %d\n", freeHeap, minFreeHeap);
      }
#ifdef DEBUG
      else {
        // Log heap status periodically for monitoring
        D_printf("Heap: %d free, %d min\n", freeHeap, minFreeHeap);
      }
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

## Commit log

2025-01-16 Added 3D printed Case
    Added Cam 3DP ESP32 case
    [SkiBeanMiniCase.3mf, SkiBeanMiniLid.3mf, SkiBeanMiniLid_nobnz.3mf]
2025-02-02 Experiment SV PID
    Experiment SV PID Use at your own risk
2025-02-20 uses interrupts to find roaster message start
2025-02-21 Added debug define to not try to use usb serial while talking to the roaster; Changed filter logic to invert test, we keep values less than 10deg apart and average the rest; Delay before calling pinm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
    [SkiBeanIOS.ino]
2025-02-21 dont track vscode
2025-02-21 show a little green led love on boot
2025-02-23 enhanced filtering added
2025-02-23 switched filter from gaussian average to median
2025-02-23 rename to show compile board target
2025-02-23 Bring medianlib filter into the repo. More elegant implementation of serial_debugging. Macro defined pin definitions so same code can support different boards.
2025-03-01 binary with smoke filter control
2025-03-01 added commands for the smoke-extractor/hat-fan
2025-03-02 Merged LED, BLE and interrupt from SkiBeanIOS to here; Swapped QuickPid library to PID_V1 due to better documentation and expected behaviors; Added CMDs for on-the-fly changes to PID tunings; Initial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
    [SkiBeanQuickSV.ino]
2025-03-04 reasonably stable version of PID control with filter and ble fixes
    [SkiBeanQuickSV.ino]
2025-03-04 return FILTER command to previous 0-4; chained filter to VENT and do the 0-100 -> 4-0 conversion there; tweak BLE timeout as it is (I think) in 10ms increments, shooting for 5 sec (previous would hav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
2025-03-06 Break up main .ino into libraries for easier reading and maintenance of code; Added BLE180A device identifier so we can show .bin build version, board and codebase
2025-03-16 v1.0.1 - make PID sample time configurable; updated README for extended PID commands; other minor fixes and additions
2025-03-16 v1.0.1 firmware bin for waveshare esp32-s3-zero with PID control
2025-04-09 v1.0.2 build and .bin PID cmds now follows TC4/Artisan format Cycle time cmd now follows TC4/Artisan format More stable PID tuning Increased median filter window from 5 to 7 Fix filter bug that shoul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
    [SkiBeanQuickSV.ino, SkiComms.h]
2025-05-09 pid and led improvements
2025-05-09 process commands and pid before transmitting message
